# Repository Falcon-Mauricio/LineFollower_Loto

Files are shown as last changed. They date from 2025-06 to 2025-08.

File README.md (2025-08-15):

# 🌸 LineFollower Loto

**Loto** es un robot seguidor de línea diseñado para competir en la disciplina de **<a href="https://lnr-argentina.com.ar/reglamentos/Reglamento%20Carrera.pdf" target="_blank">Carrera</a>** (fondo negro con línea blanca) organizada por la **<a href="https://lnr-argentina.com.ar/" target="_blank">LNR</a>**. Su diseño está inspirado en los pétalos de una flor loto.

<div align="center">
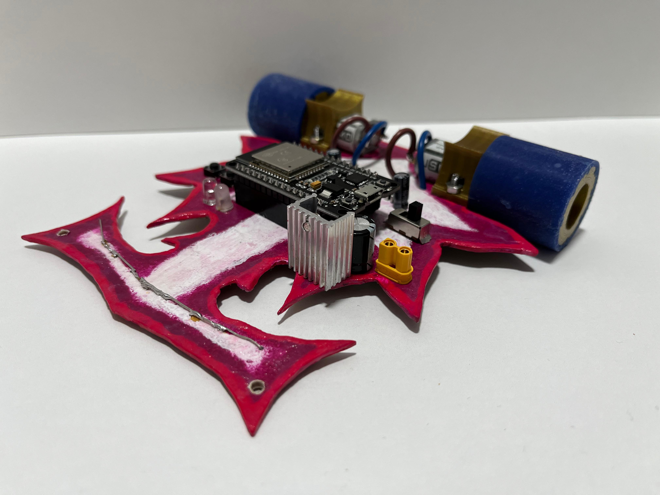
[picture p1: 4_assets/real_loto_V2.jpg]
VistaInferior_Loto
  
</div>

<div align="center" style="display: flex; justify-content: center; gap: 10px; margin-top: 10px;">
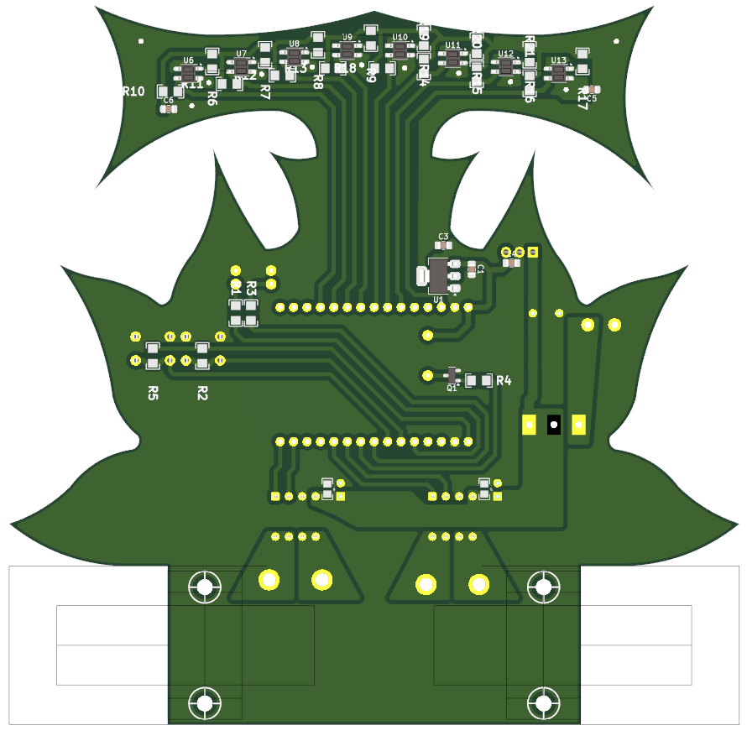
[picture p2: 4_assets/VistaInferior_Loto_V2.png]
VistaInferior_Loto_V2
  
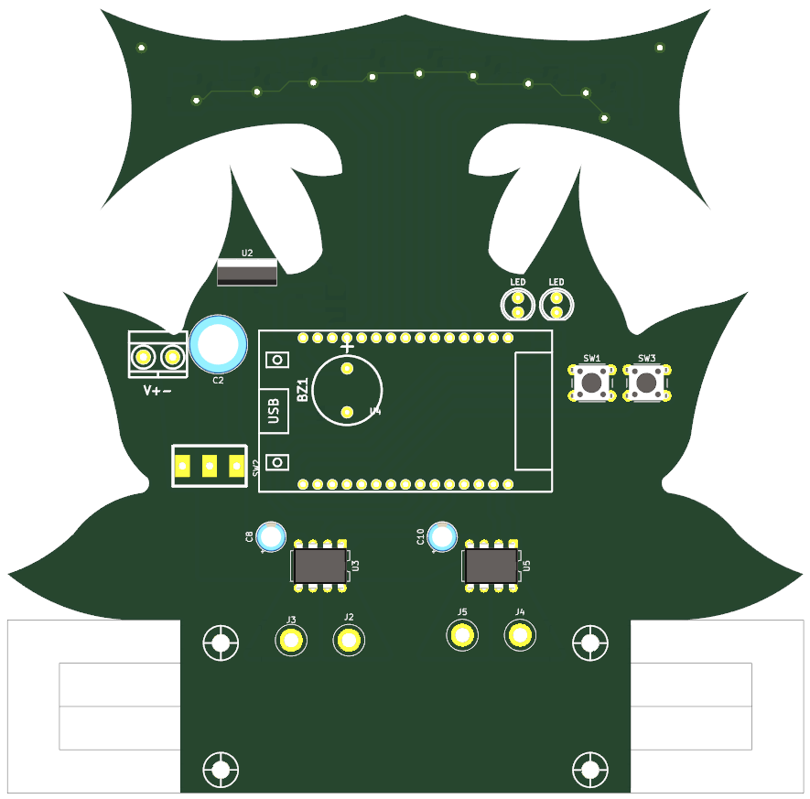
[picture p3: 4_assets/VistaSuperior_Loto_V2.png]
VistaSuperior_Loto
  
</div>

---

## 🚀 Características principales

| Especificación | Detalle |
|---|---|
| **Dimensiones** | 138 mm (ancho) x 136 mm (largo) |
| **Chasis** | PCB estructural + soporte de motores impreso en PLA |
| **Batería** | LiPo 3S 350 mAh |
| **Microcontrolador** | ESP32 |
| **Sensores** | 8 sensores QRE (QRE1113GR) |
| **Motores** | ProFast 12V 3600 RPM |
| **Driver de motores** | TA6586 |

---

## ⚡ Entradas / Salidas (I/O)

<table>
<tr>

<td>

### Entradas (sensores y botones)

| Pin ESP32 | Descripción |
|---|---|
| GPIO13 | QRE sensor 1 |
| GPIO27 | QRE sensor 2 |
| GPIO26 | QRE sensor 3 |
| GPIO25 | QRE sensor 4 |
| GPIO33 | QRE sensor 5 |
| GPIO32 | QRE sensor 6 |
| GPIO35 | QRE sensor 7 |
| GPIO34 | QRE sensor 8 |
| GPIO17 | Pulsador 1 |
| GPIO16 | Pulsador 2 |

</td>

<td>

### Salidas (motores y otros)

| Pin ESP32 | Descripción |
|---|---|
| GPIO19 | PWM A Motor 1 |
| GPIO21 | PWM B Motor 1 |
| GPIO22 | PWM A Motor 2 |
| GPIO23 | PWM B Motor 2 |
| GPIO04 | LED 1 |
| GPIO05 | LED 2 |
| GPIO18 | BUZZER |

</td>

</tr>
</table>

---

## 🛠 Tecnologías utilizadas

- **FreeCAD** → Diseño mecánico del soporte de motores y elementos impresos
- **KiCad** → Diseño del PCB
- **PlatformIO VisualStudioCODE** → Firmware para el ESP32

---

## 📂 Archivos

- `1_hardware_pcb/` → Archivos de KiCad (PCB + esquemas)  
- `2_hardware_3d/` → Archivos FreeCAD / STL de las piezas impresas
- `3_firmware/` → Código fuente para el ESP32
- `4_assets/` → Fotos y videos del robot  
- `docs/` → Diagramas, esquemas y documentación

---

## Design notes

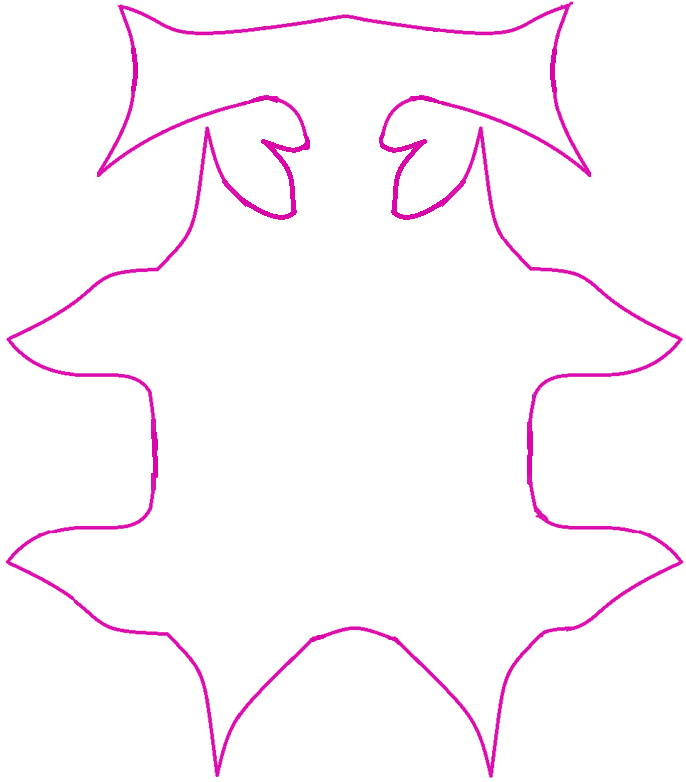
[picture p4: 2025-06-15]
2_hardware_3d/Sketch_Reference/LotoBoceto_Final.png

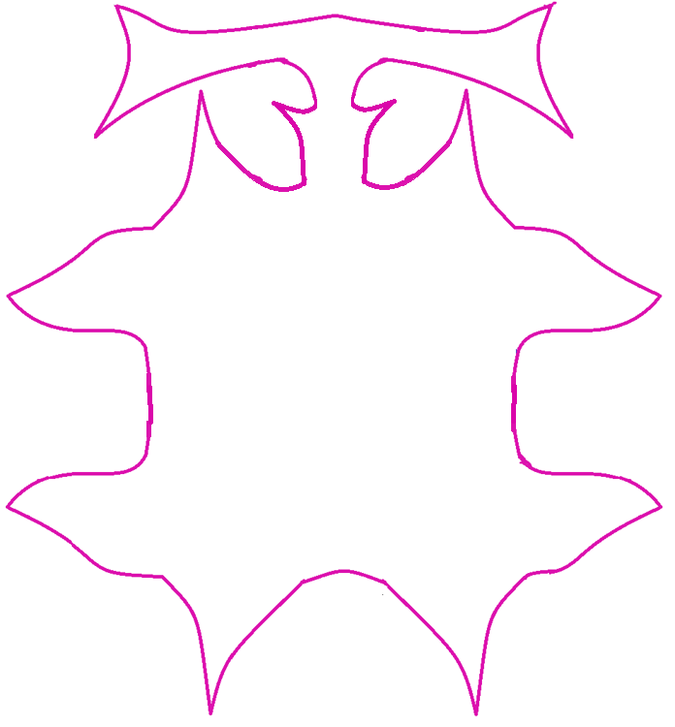
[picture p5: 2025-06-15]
2_hardware_3d/Sketch_Reference/LotoBoceto_3.png

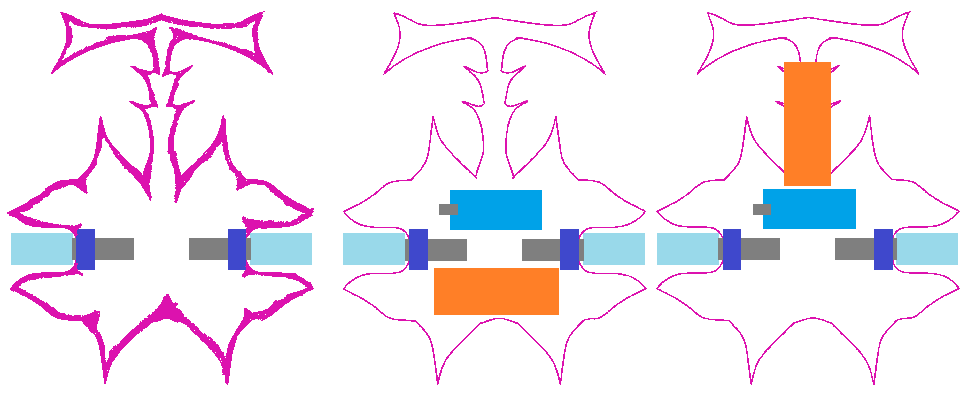
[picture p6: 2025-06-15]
2_hardware_3d/Sketch_Reference/LotoConcepto.png

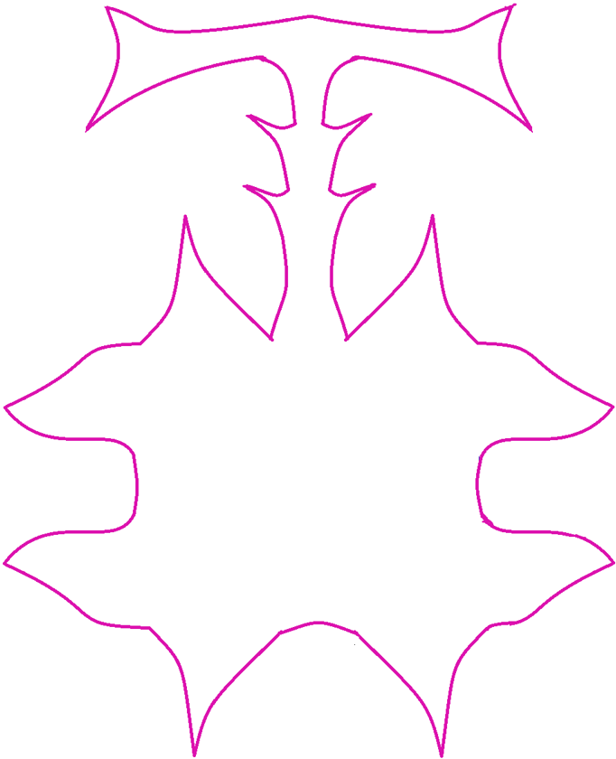
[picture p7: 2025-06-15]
2_hardware_3d/Sketch_Reference/LotoBoceto_1.png

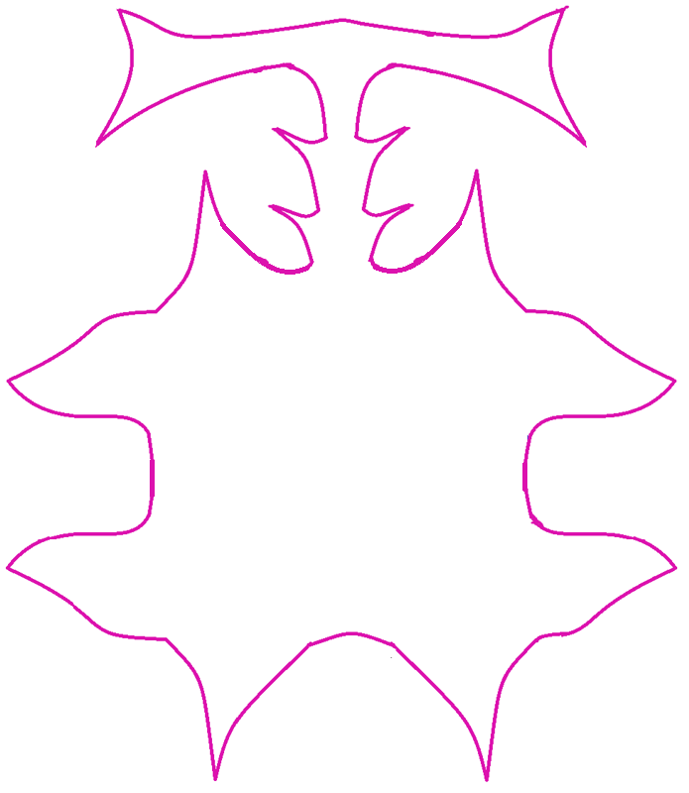
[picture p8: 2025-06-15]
2_hardware_3d/Sketch_Reference/LotoBoceto_2.png

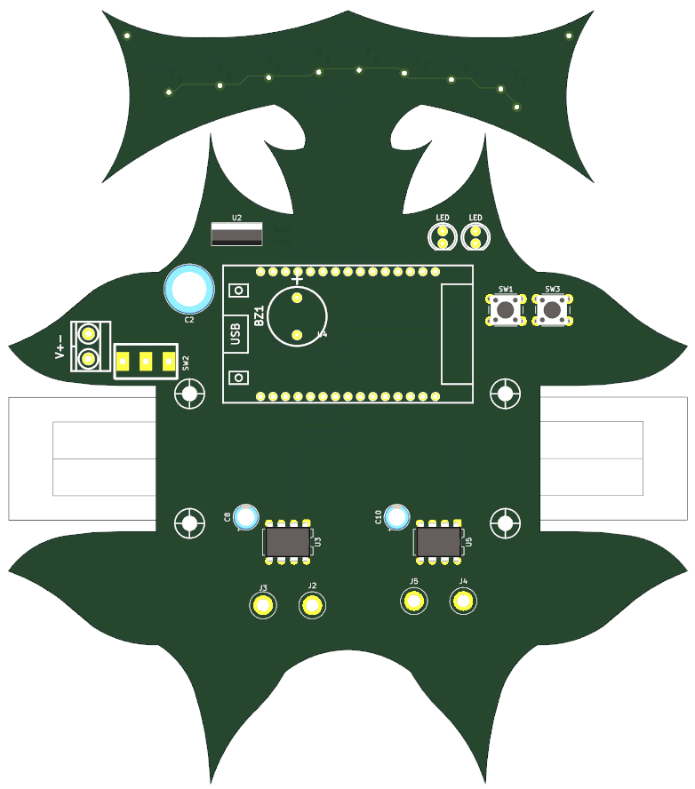
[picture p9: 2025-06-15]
4_assets/VistaSuperior_Loto.png

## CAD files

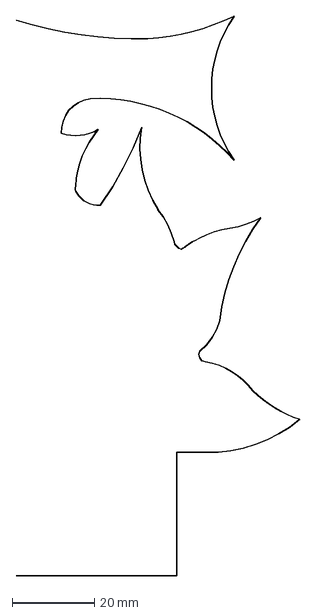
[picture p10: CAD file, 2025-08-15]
1_hardware_pcb/Main_Board_Loto_V2/fabrication/Skech_lotoV2.dxf
69.0 x 136.0 mm

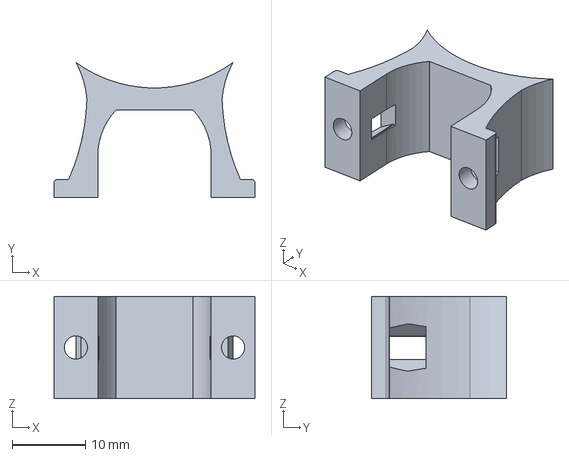
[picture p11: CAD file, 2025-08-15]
2_hardware_3d/Braquet/BraquetMotorProFast.FCStd
27.5 x 18.5 x 14.0 mm

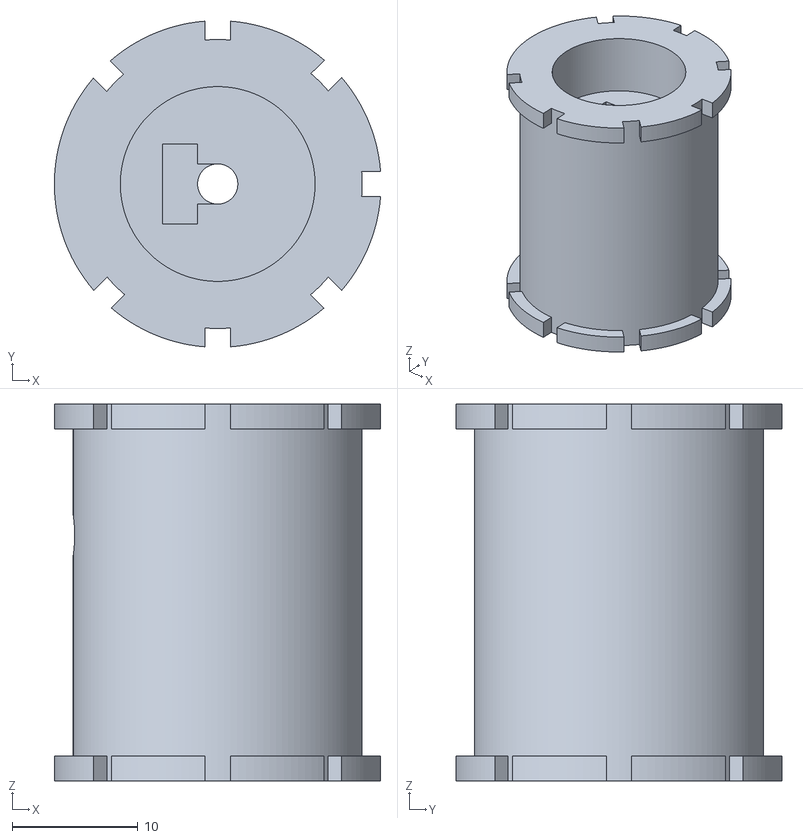
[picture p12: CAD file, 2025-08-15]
2_hardware_3d/Rueda/Rueda-Llanta.stl
26.0 x 25.9 x 30.0

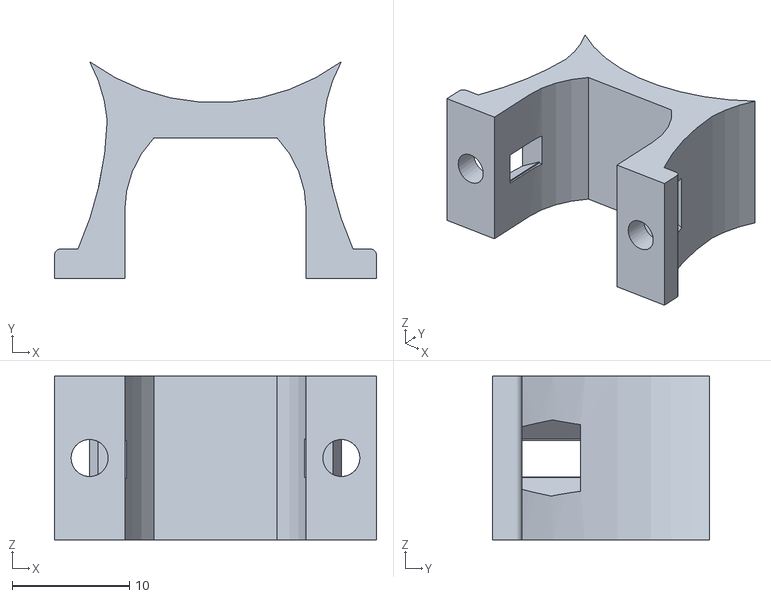
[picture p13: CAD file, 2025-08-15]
2_hardware_3d/Braquet/BraquetMotorProFast-BraquetMotor001BraquetMotor.stl
27.5 x 18.5 x 14.0

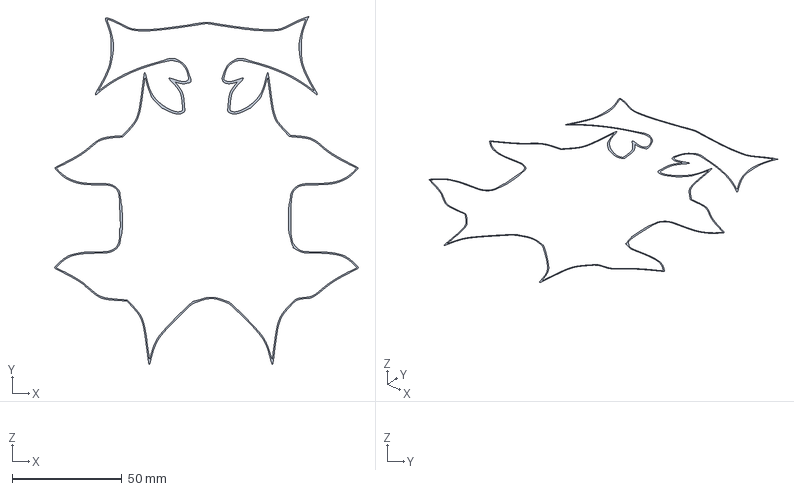
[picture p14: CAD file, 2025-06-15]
2_hardware_3d/pcb_layout/PCB_Layout.FCStd
138.7 x 158.6 x 0 mm

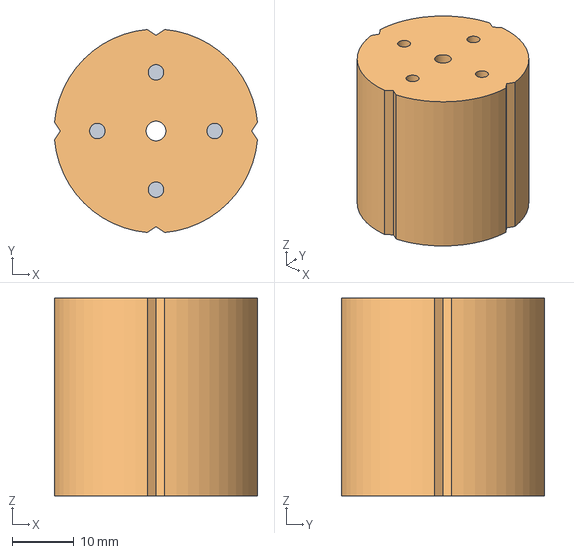
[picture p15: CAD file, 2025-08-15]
2_hardware_3d/Rueda/Rueda.FCStd
32.9 x 32.9 x 32.0 mm
Llanta
MoldeCubierta

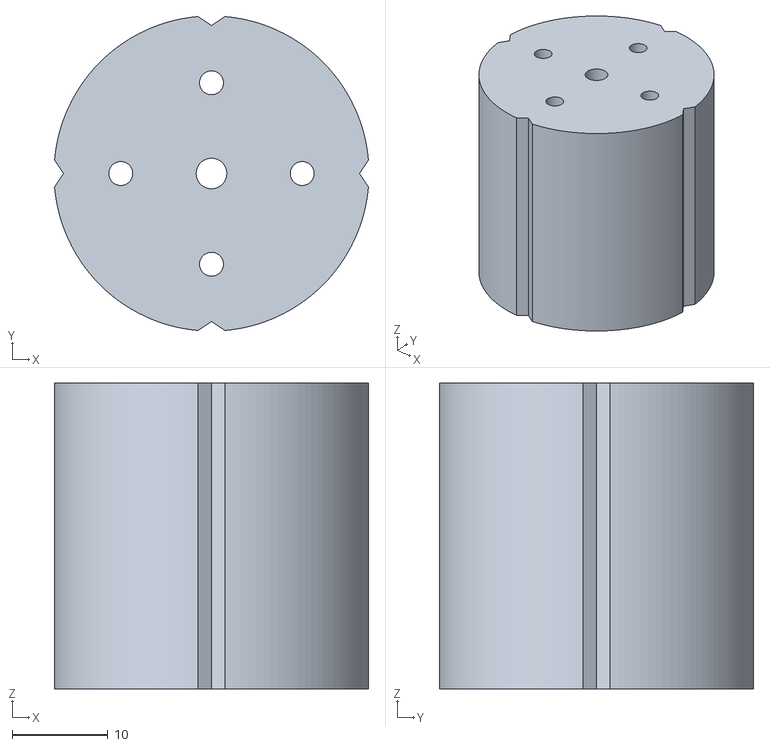
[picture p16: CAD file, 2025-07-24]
2_hardware_3d/Rueda/Rueda-PartMoldeCubierta.stl
32.9 x 32.9 x 32.0

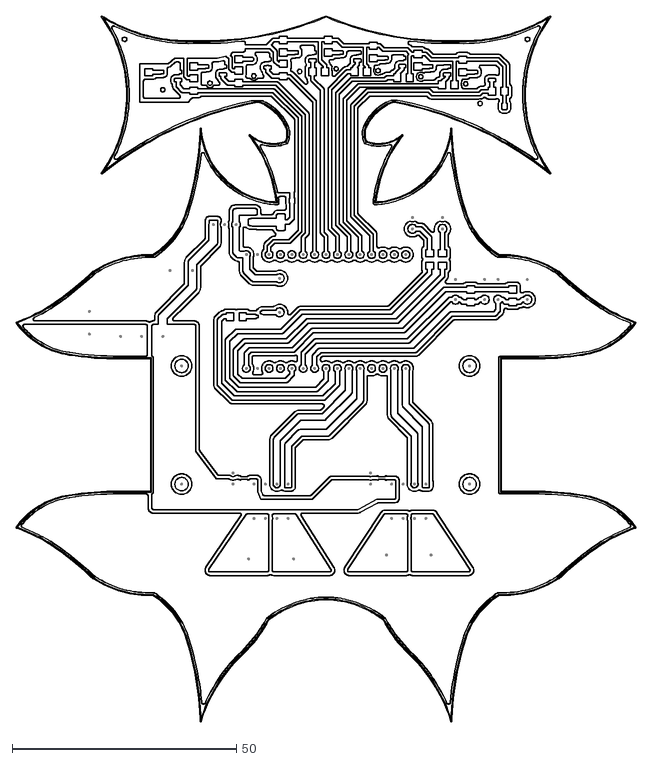
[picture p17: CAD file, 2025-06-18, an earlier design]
1_hardware_pcb/Main_Board_Loto/Fabrication/Main_Board_Loto-B_Cu.dxf
138.2 x 157.5

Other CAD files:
2_hardware_3d/pcb_layout/Sketch_refernceLotoV2.FCStd

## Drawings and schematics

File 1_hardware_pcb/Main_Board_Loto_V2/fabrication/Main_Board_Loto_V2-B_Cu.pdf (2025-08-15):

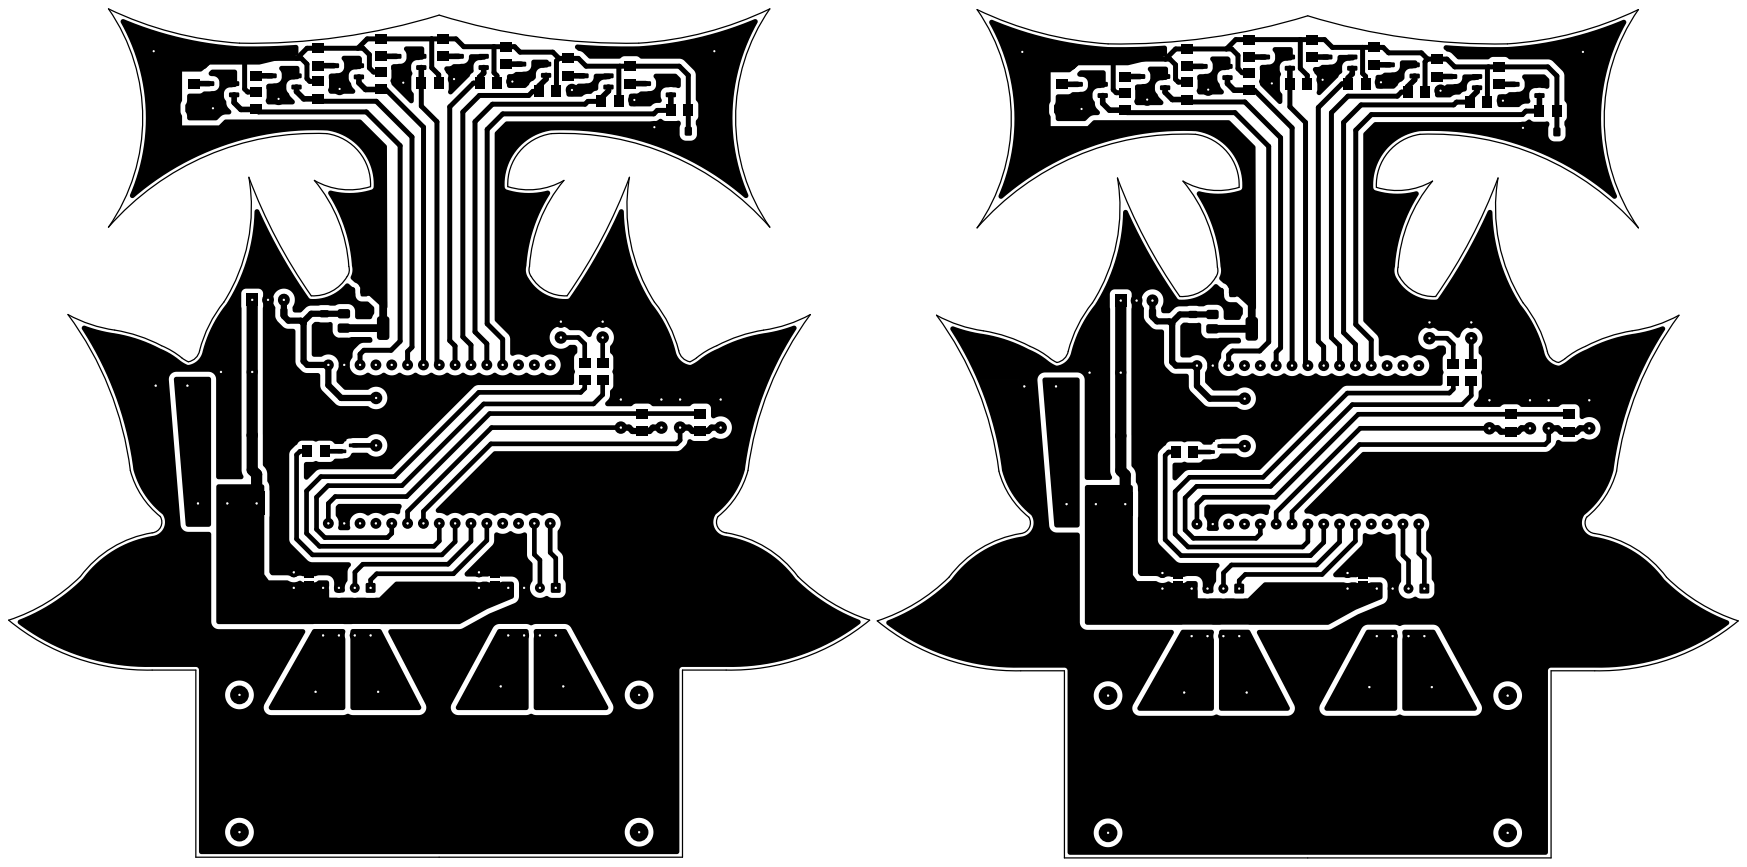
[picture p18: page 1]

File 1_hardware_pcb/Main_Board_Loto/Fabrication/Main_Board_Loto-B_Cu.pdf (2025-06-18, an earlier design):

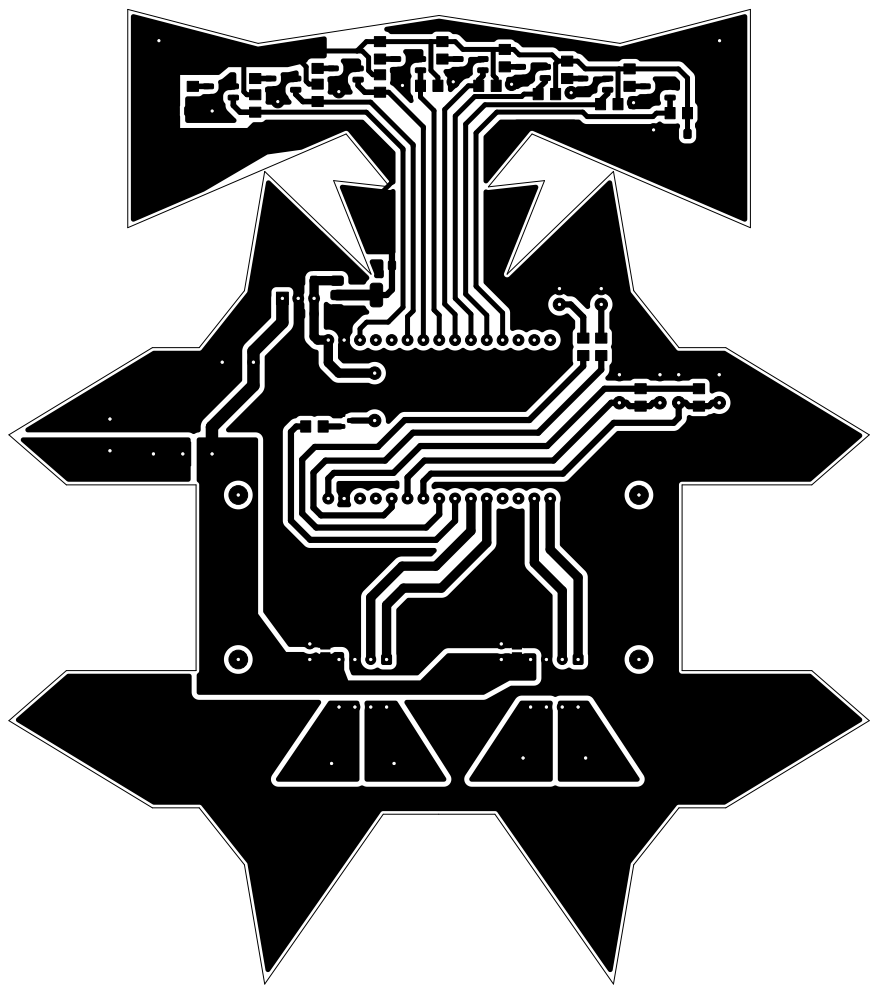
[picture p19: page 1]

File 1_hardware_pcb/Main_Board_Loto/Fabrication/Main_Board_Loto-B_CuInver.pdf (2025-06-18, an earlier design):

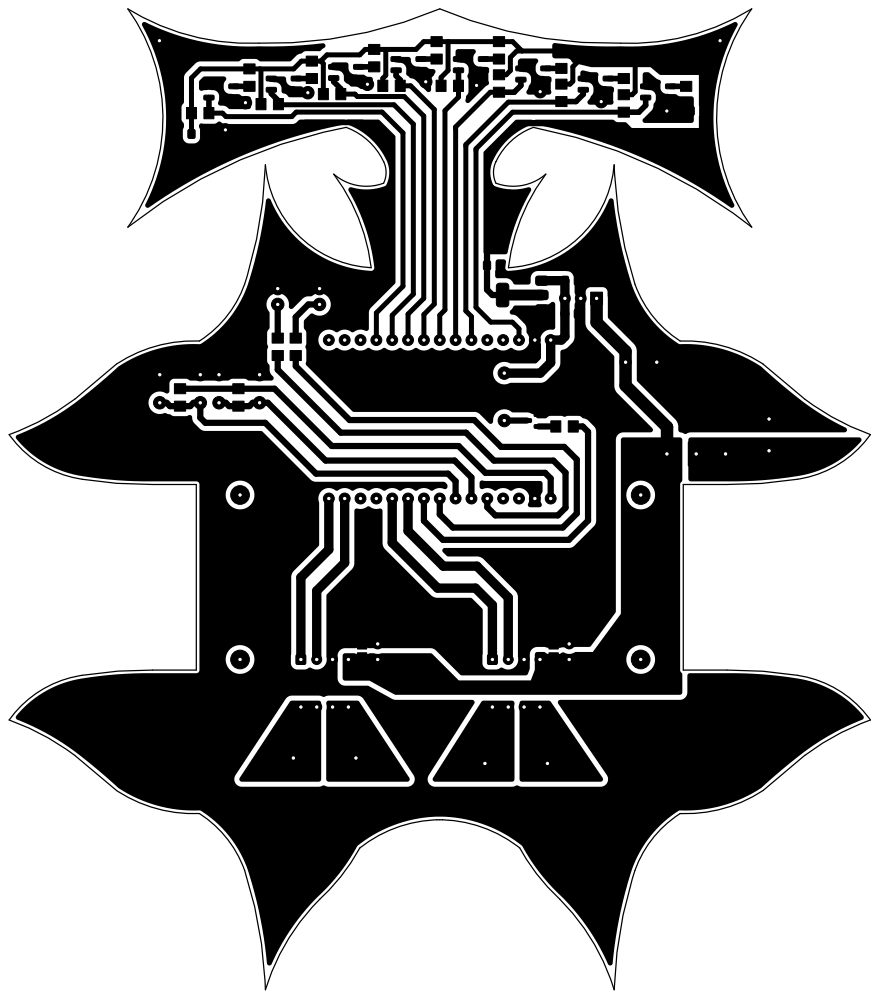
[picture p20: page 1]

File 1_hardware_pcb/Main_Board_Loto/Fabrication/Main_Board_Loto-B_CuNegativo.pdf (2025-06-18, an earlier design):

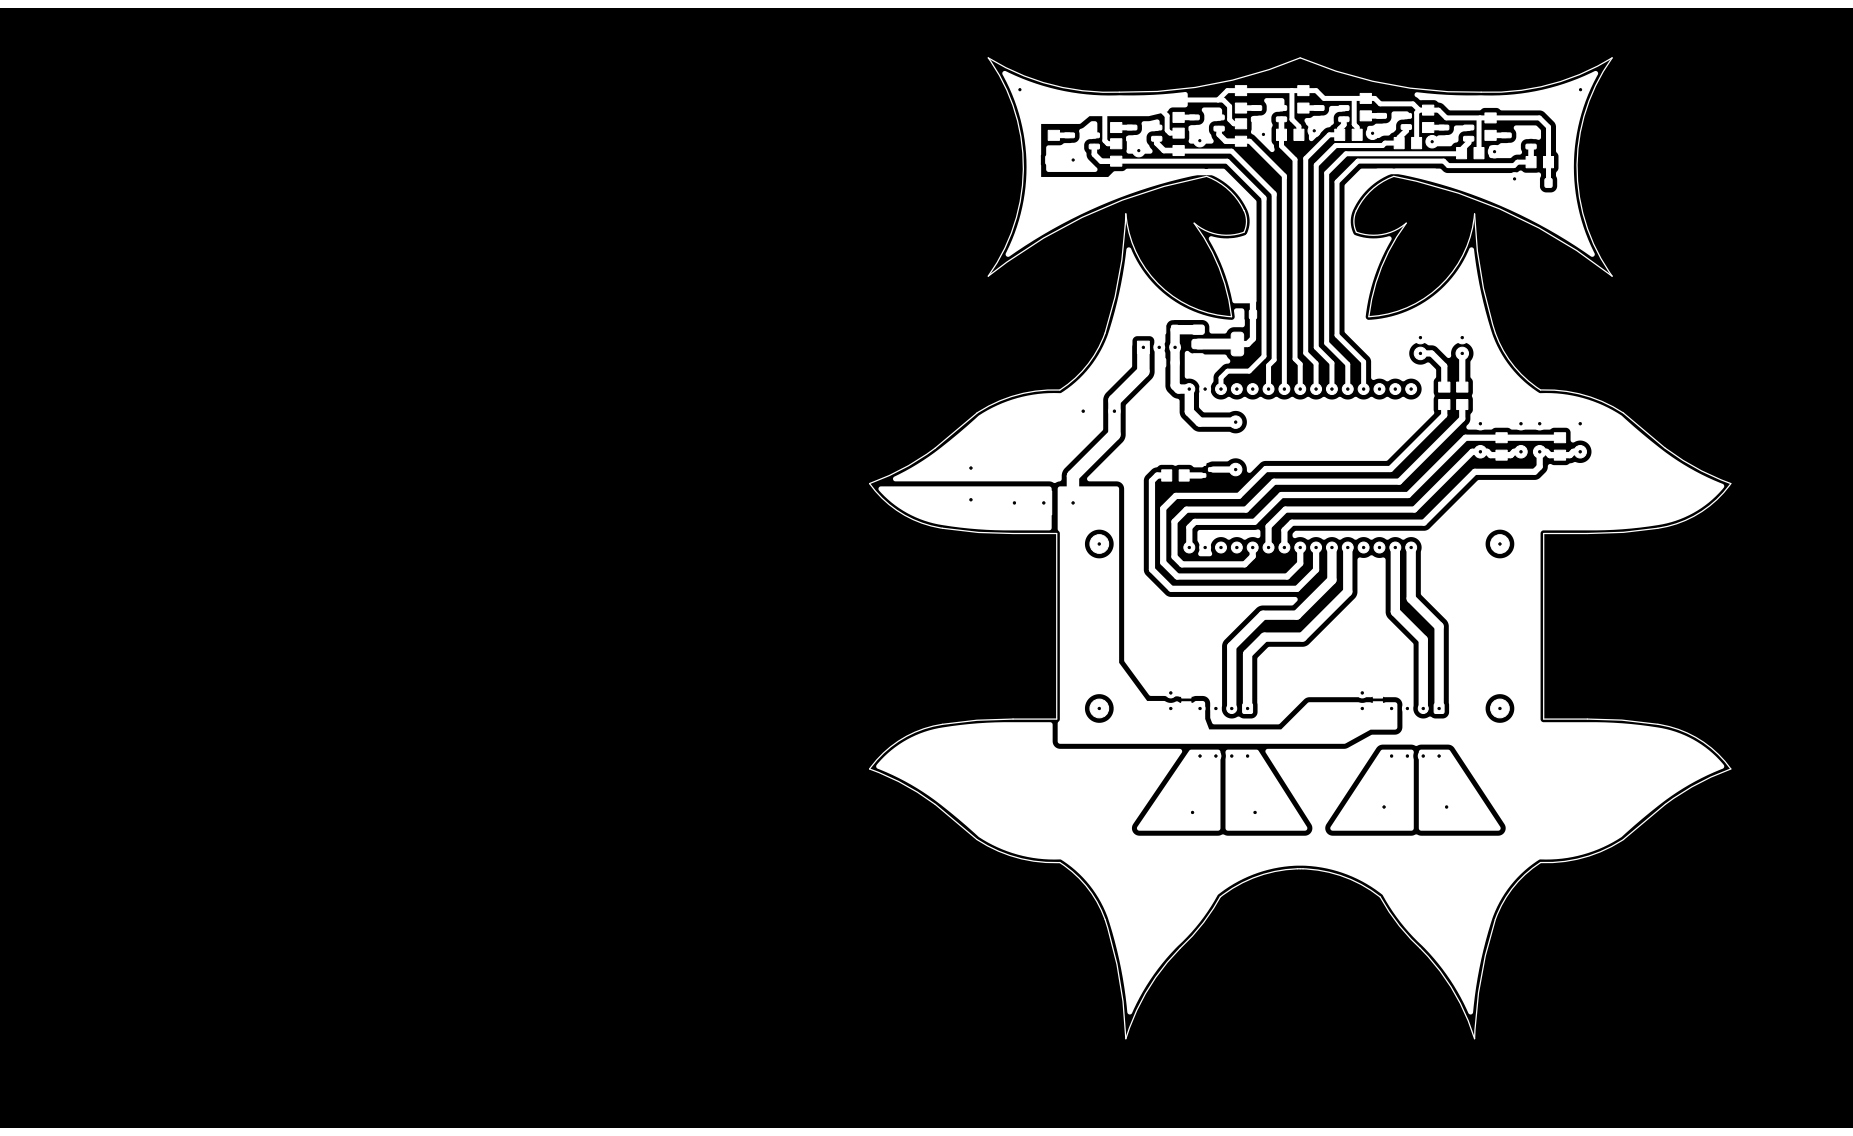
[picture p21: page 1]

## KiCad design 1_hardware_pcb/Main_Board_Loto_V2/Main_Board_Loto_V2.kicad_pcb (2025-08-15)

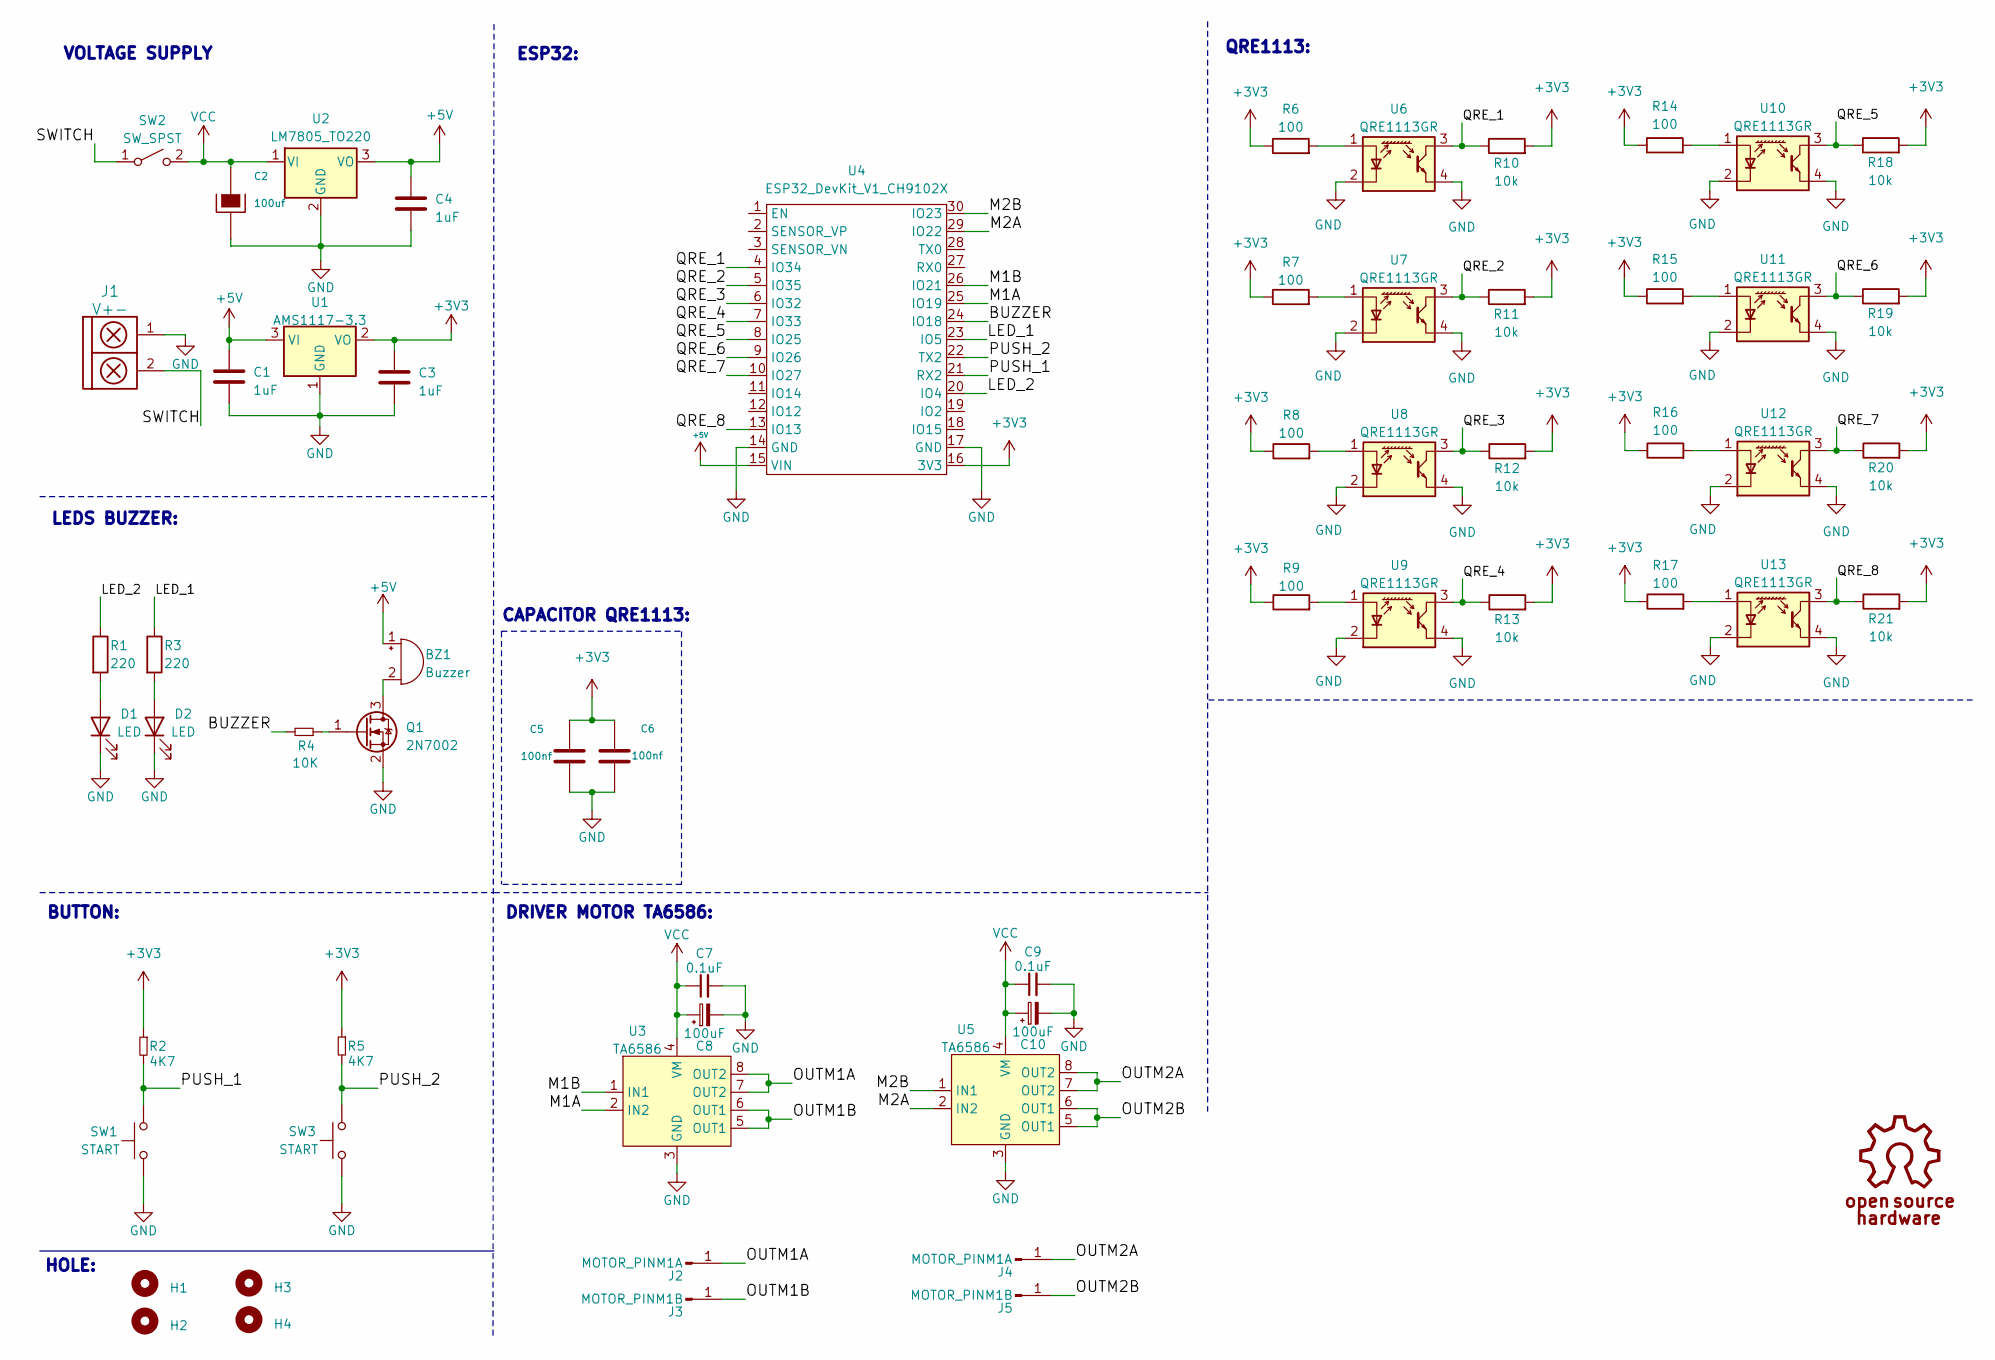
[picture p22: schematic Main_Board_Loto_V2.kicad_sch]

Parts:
BZ1: Buzzer; Buzzer_12mm
C1, C3, C4: 1uF; C_0805_2012Metric_Pad1.18x1.45mm_HandSolder
C2: 100uf; C_Radial_D10.0mm_H12.5mm_P5.00mm
C5, C6: 100nf; C_0805_2012Metric_Pad1.18x1.45mm_HandSolder
C7, C9: 0.1uF; C_0805
C8, C10: 100uF; CP_Radial_D5.0mm_P2.50mm
D1, D2: LED; led_5mm_clear
H1, H2, H3, H4: Mounting_Hole; hole_3mm
J1: V+-; BORNERA2_AZUL
J2, J4: MOTOR_PINM1A; Banana_Jack_1Pin
J3, J5: MOTOR_PINM1B; Banana_Jack_1Pin
Q1: 2N7002; SOT-23
R1, R3: 220; R_1206
R2, R5: 4K7; R_1206
R4: 10K; R_1206
R6, R7, R8, R9, R14, R15, R16, R17: 100; R_1206
R10, R11, R12, R13, R18, R19, R20, R21: 10k; R_1206
SW1, SW3: START; SW_PUSH_6mm_H5mm
SW2: SW_SPST; SW_SPDT_TH_Vertical
U1: AMS1117-3.3; SOT-223-3_TabPin2
U2: LM7805_TO220; TO-220-3_Vertical
U3, U5: TA6586; DIP-8_W7.62mm
U4: ESP32_DevKit_V1_CH9102X
U6, U7, U8, U9, U10, U11, U12, U13: QRE1113GR; OnSemi_CASE100CY

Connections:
+3V3: C3.1, C5.1, C6.1, R2.1, R5.1, R6.1, R7.1, R8.1, R9.1, R10.2, R11.2, R12.2, R13.2, R14.1, R15.1, R16.1, R17.1, R18.2, R19.2, R20.2, R21.2, U1.2 (VO), U4.16 (3V3)
+5V: BZ1.1 (-), C1.1, C4.1, U1.3 (VI), U2.3 (VO), U4.15 (VIN)
/BUZZER: R4.2, U4.24 (IO18)
/LED_1: R3.1, U4.23 (IO5)
/LED_2: R1.1, U4.20 (IO4)
/M1A: U3.2 (IN2), U4.25 (IO19)
/M1B: U3.1 (IN1), U4.26 (IO21)
/M2A: U4.29 (IO22), U5.2 (IN2)
/M2B: U4.30 (IO23), U5.1 (IN1)
/OUTM1A: J2.1, U3.7 (OUT2), U3.8 (OUT2)
/OUTM1B: J3.1, U3.5 (OUT1), U3.6 (OUT1)
/OUTM2A: J4.1, U5.7 (OUT2), U5.8 (OUT2)
/OUTM2B: J5.1, U5.5 (OUT1), U5.6 (OUT1)
/PUSH_1: R2.2, SW1.2, U4.21 (RX2)
/PUSH_2: R5.2, SW3.2, U4.22 (TX2)
/QRE_1: R10.1, U4.4 (IO34), U6.3
/QRE_2: R11.1, U4.5 (IO35), U7.3
/QRE_3: R12.1, U4.6 (IO32), U8.3
/QRE_4: R13.1, U4.7 (IO33), U9.3
/QRE_5: R18.1, U4.8 (IO25), U10.3
/QRE_6: R19.1, U4.9 (IO26), U11.3
/QRE_7: R20.1, U4.10 (IO27), U12.3
/QRE_8: R21.1, U4.13 (IO13), U13.3
/SWITCH: J1.2, SW2.1 (A)
GND: C1.2, C2.2, C3.2, C4.2, C5.2, C6.2, C7.2, C8.2, C9.2, C10.2, D1.1 (K), D2.1 (K), J1.1, Q1.2 (S), SW1.1, SW3.1, U1.1 (GND), U2.2 (GND), U3.3 (GND), U4.14 (GND), U4.17 (GND), U5.3 (GND), U6.2 (K), U6.4, U7.2 (K), U7.4, U8.2 (K), U8.4, U9.2 (K), U9.4, U10.2 (K), U10.4, U11.2 (K), U11.4, U12.2 (K), U12.4, U13.2 (K), U13.4
unnamed: BZ1.2 (+), Q1.3 (D)
unnamed: D1.2 (A), R1.2
unnamed: D2.2 (A), R3.2
unnamed: Q1.1 (G), R4.1
unnamed: R6.2, U6.1 (A)
unnamed: R7.2, U7.1 (A)
unnamed: R8.2, U8.1 (A)
unnamed: R9.2, U9.1 (A)
unnamed: R14.2, U10.1 (A)
unnamed: R15.2, U11.1 (A)
unnamed: R16.2, U12.1 (A)
unnamed: R17.2, U13.1 (A)
VCC: C2.1, C7.1, C8.1, C9.1, C10.1, SW2.2 (B), U2.1 (VI), U3.4 (VM), U5.4 (VM)

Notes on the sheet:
ESP32:
CAPACITOR QRE1113:
HOLE:
VOLTAGE SUPPLY
BUTTON:
LEDS BUZZER:
QRE1113:
DRIVER MOTOR TA6586:

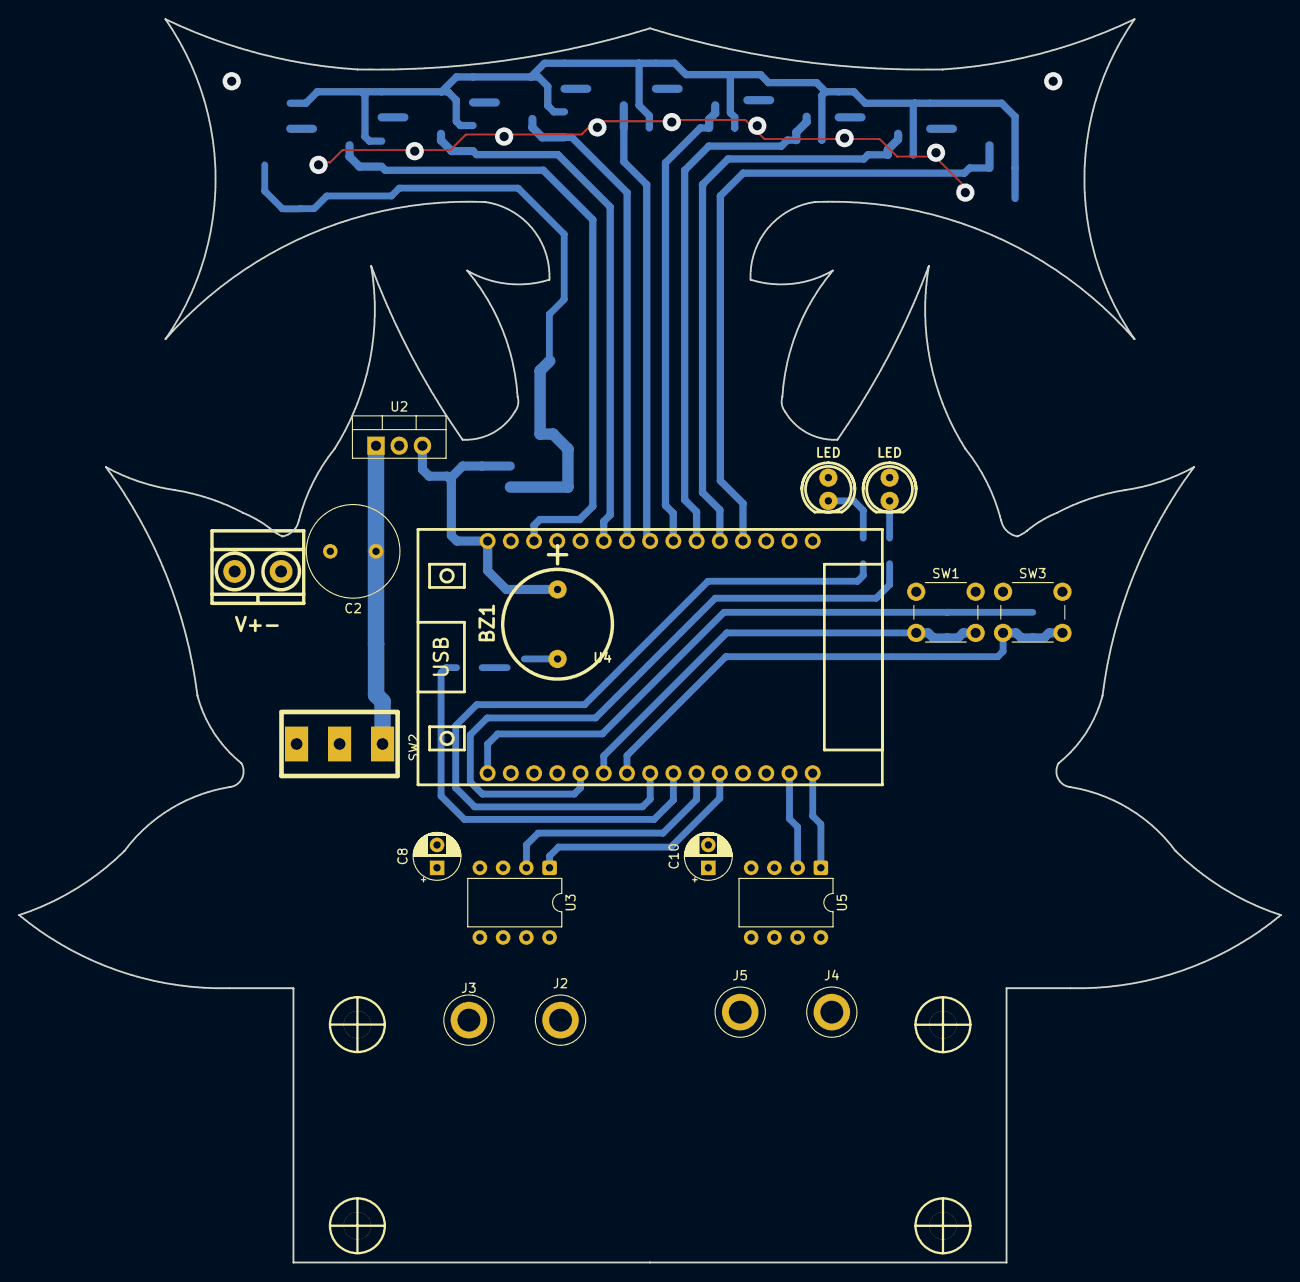
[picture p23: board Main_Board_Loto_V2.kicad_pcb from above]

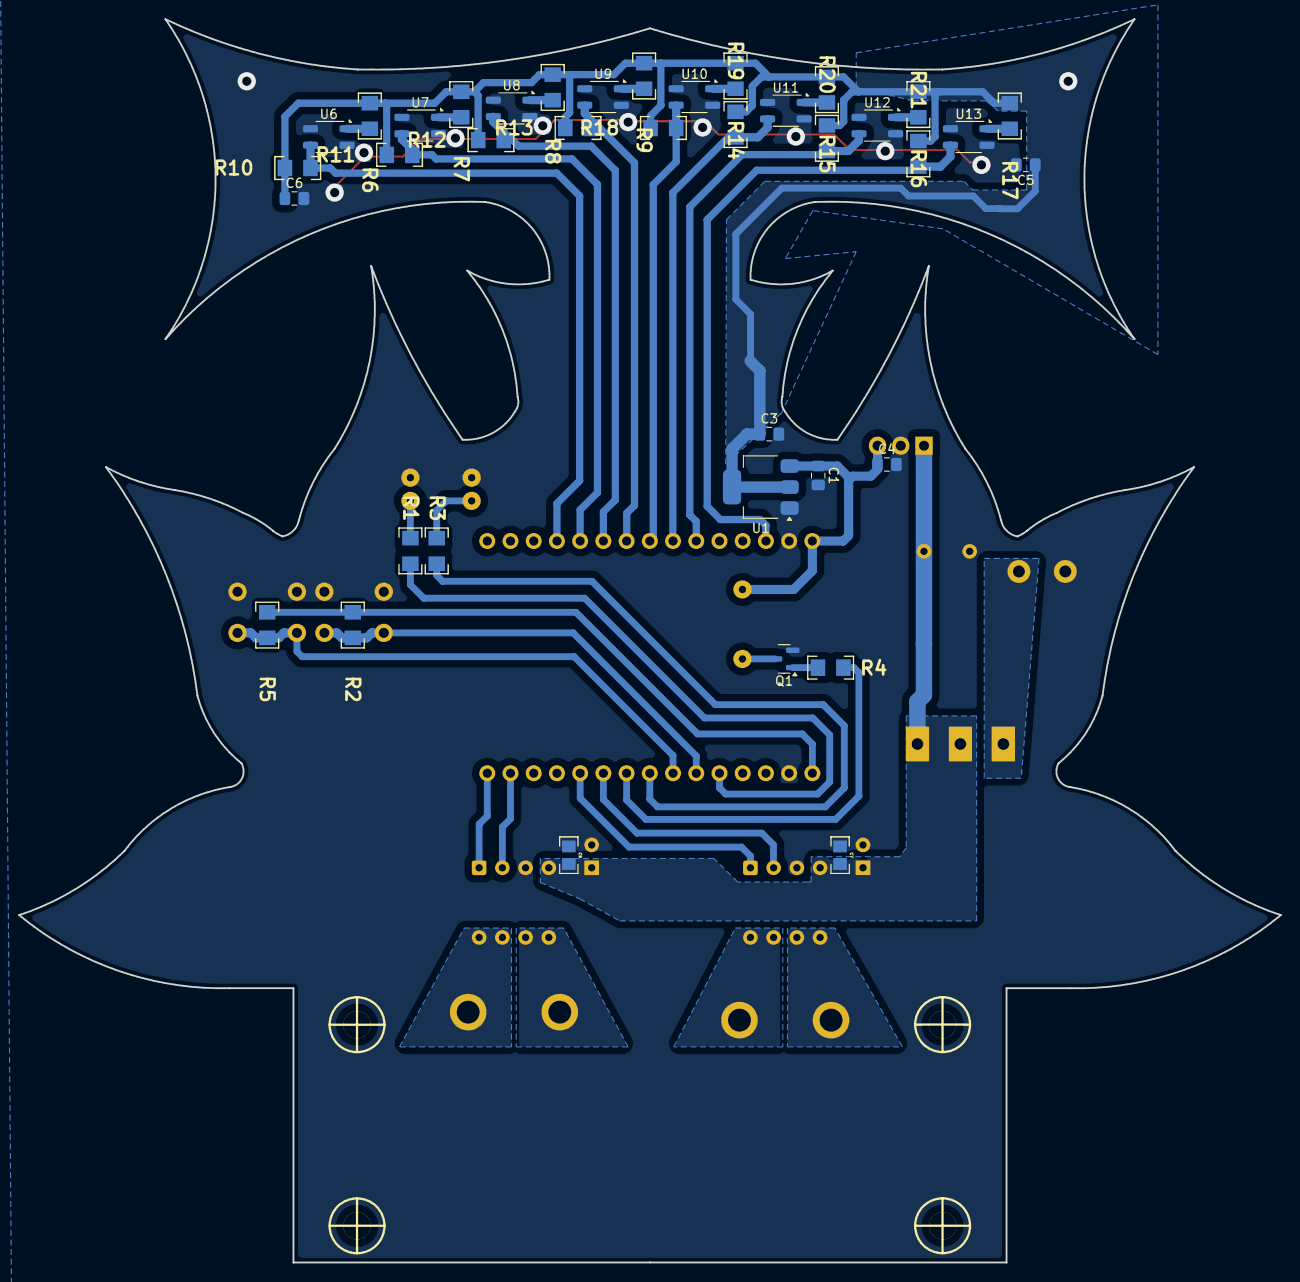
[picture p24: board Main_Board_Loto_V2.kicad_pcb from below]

Board: 2 copper layers, 138.0 x 136.0 mm, 60 parts (38 on the bottom side), 38 nets.

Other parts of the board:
H3#2, H4#2: Mounting_Hole; hole_3mm

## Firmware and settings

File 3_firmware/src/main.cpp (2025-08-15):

#include <Arduino.h>

// Pines motores
const int IN1_A = 19;
const int IN2_A = 21;
const int IN1_B = 22;
const int IN2_B = 23;

// Canales PWM
const int canalA1 = 0;
const int canalA2 = 1;
const int canalB1 = 2;
const int canalB2 = 3;

// Configuración PWM
const int frecuenciaPWM = 8000;   // 8 kHz
const int resolucionPWM = 12;     // 12 bits
const int PWM_mitad = 1028;       // 50% de 4095

void detenerMotores() {
  ledcWrite(canalA1, 0);
  ledcWrite(canalA2, 0);
  ledcWrite(canalB1, 0);
  ledcWrite(canalB2, 0);
}

void avanzar() {
  ledcWrite(canalA1, PWM_mitad);
  ledcWrite(canalA2, 0);

  ledcWrite(canalB1, PWM_mitad);
  ledcWrite(canalB2, 0);
}

void retroceder() {
  ledcWrite(canalA1, 0);
  ledcWrite(canalA2, PWM_mitad);

  ledcWrite(canalB1, 0);
  ledcWrite(canalB2, PWM_mitad);
}

void setup() {
  // Configurar canales PWM
  ledcSetup(canalA1, frecuenciaPWM, resolucionPWM);
  ledcSetup(canalA2, frecuenciaPWM, resolucionPWM);
  ledcSetup(canalB1, frecuenciaPWM, resolucionPWM);
  ledcSetup(canalB2, frecuenciaPWM, resolucionPWM);

  // Asociar pines con canales
  ledcAttachPin(IN1_A, canalA1);
  ledcAttachPin(IN2_A, canalA2);
  ledcAttachPin(IN1_B, canalB1);
  ledcAttachPin(IN2_B, canalB2);

  Serial.begin(115200);
}

void loop() {
  Serial.println("Avanzando...");
  avanzar();
  delay(3000);

  Serial.println("Detenido...");
  detenerMotores();
  delay(1000);

  Serial.println("Retrocediendo...");
  retroceder();
  delay(3000);

  Serial.println("Detenido...");
  detenerMotores();
  delay(1000);
}

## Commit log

2025-06-09 Creacion del proyecto kicad para el PCB
    [Main_Board_Loto.kicad_pcb, Main_Board_Loto.kicad_sch]
2025-06-09 SCH terminado
    [Main_Board_Loto.kicad_pcb, Main_Board_Loto.kicad_sch]
2025-06-11 Definida la ubicacion de los componentes y enrutadas las vias de los mismos
    [Main_Board_Loto.kicad_pcb]
2025-06-15 Cntorno de PCB diseñad en FreeCAD y PCB terminad en Kicad
    [Main_Board_Loto.kicad_pcb, Main_Board_Loto.kicad_sch, PCB_Layout.FCStd]
2025-06-15 Soporte para motor incluido en el PCB y generadas las imagenes de fabricacion
    [Main_Board_Loto.kicad_pcb]
2025-06-17 Pistas de 0.75 pasaron a 0.8 por temas de CNC
    [Main_Board_Loto.kicad_pcb]
2025-06-18 Generacion de PDF y SVG para fabricacion en CNC
    [Main_Board_Loto-B_Cu.dxf, Main_Board_Loto.kicad_pcb]
2025-07-22 Diseñado el Soporte para motor ProFast
    [BraquetMotorProFast-BraquetMotor001BraquetMotor.stl, BraquetMotorProFast.FCStd]
2025-07-23 Diseñada la llante para rueda de 30x30
    [Rueda-PartCuerpo.stl, Rueda.FCStd]
2025-07-24 Diseñado el molde para la cubierta de 30x30
    [Rueda-Llanta.stl, Rueda-PartCuerpo.stl, Rueda-PartMoldeCubierta.stl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]
2025-08-15 Cambie la placa generando la V2 y ordene el repo
    [BraquetMotorProFast-BraquetMotor001BraquetMotor.stl, BraquetMotorProFast.FCStd, Main_Board_Loto_V2.kicad_pcb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]
